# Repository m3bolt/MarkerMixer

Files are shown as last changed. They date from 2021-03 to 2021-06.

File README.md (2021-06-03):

<!-- PROJECT LOGO -->
<br />
<p align="center">
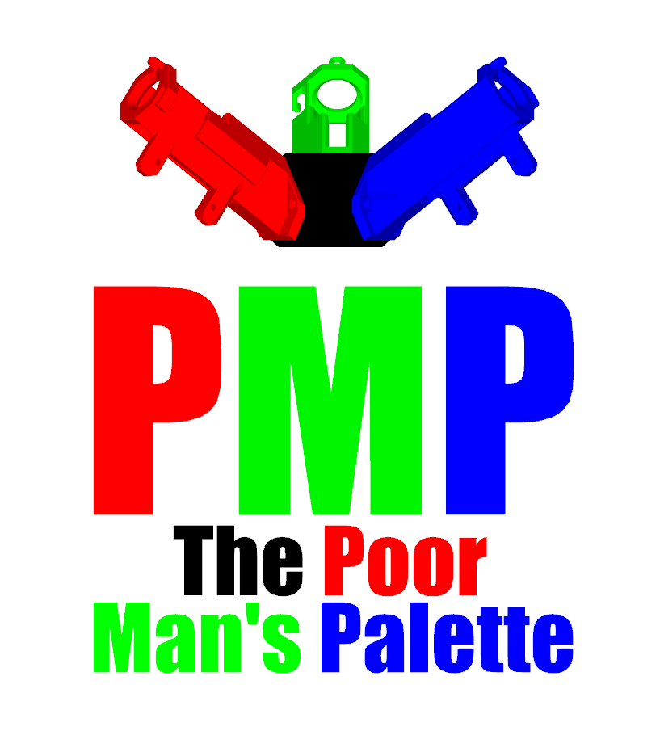
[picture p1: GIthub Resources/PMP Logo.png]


  <p align="center">
   Marker mixer/blender for dying filament with permanent markers before it enters the hotend
    <br />
	<a href="https://discord.gg/TchtRx5vXf"><strong>Join the PMP Discord </strong></a>
	·
    <a href="https://github.com/m3bolt/MarkerMixer/tree/main/STLs"><strong>Download STLs </strong></a>
	·
    <a href="https://www.youtube.com/watch?v=Sshl-3-f8Ro"><strong>PMP Demo Video </strong></a>
    ·
    <a href="https://github.com/m3bolt/MarkerMixer/issues">Report Bug</a>
    ·
    <a href="https://github.com/m3bolt/MarkerMixer/issues">Request Feature</a>
  </p>
</p>

<!-- ABOUT THE PROJECT -->
## About The Project

The Poor Mans Palette is designed to use servos to slide markers in out and of a central filament path. It is an evolution of and directly inspired by Youtuber Makers Muse who designed a manual version.

<!-- GETTING STARTED -->
## Getting Started

Using the Poor Mans Palette is easy, but it does require some setup. <a href="https://github.com/kackle1998">Viperian</a> has created <a href="https://docs.google.com/document/d/1HtXDXiIX8TrwlF5AgzMKKhFVkw75yK6E26BhG-3SkN0/edit"><strong>Google Doc Instructions</strong></a> for new users to set up and use their PMP. 

You will need some electronics and hardware:

| Part Name | Description | Quantity |
| --- | --- | --- |
| 3D Printer running Klipper | Klipper is required for servo control | 1 |
| Arduino (Nano or Uno)  | Used by Klipper to address servo pins  | 1 |
| 5v 1A+ Power Supply | Necessary to power servos, barrel jack recommended | 1 |
| M3 x 10mm screw | To secure Marker Holder to Marker Hub | 6 |
| M3 x 12mm screw | To hold the marker in in the Marker Slider | 3 |
| M3 Locknut | To secure Marker Screw Cap to 12mm screw | 3 | 
| M3 x 16mm screw | To mount Marker Hub to your printers Hub Mount | 3 |
| Breadboard or Perfboard | Used for wiring servos to the Arduino | 1 |
| 3-pin DUPONT headers | For plugging the servos into your breadboard or perfboard | 3 |
| SG90 Servo Motor | Used to extend and retract the markers | 3 |
| SG90 Servo mounting screws | Usually included with your SG90, these secure the servo to the Marker Body | 6 |

The following are the STLs required for a 3 marker setup and the quantity of each required: 

| Part Name | Notes | Quantity |
| --- | --- | --- |
| PMP_MarkerHub_R1.stl | | 1 |
| PMP_MarkerBody_NumX_R1.stl | Requires supports! Print NoNum for no numbers or 1-3 for numbered versions. | 3 |
| PMP_MarkerSlider_Size_ID_R1.stl | 2 versions available, one with a smaller ID and one with a larger ID. Print one at a time to verify the size required! | 3 |
| PMP_ServoGear_Size_ID_R1.stl | 5 versions available with different IDs for the servo shaft. Print one at a time to verify the size required! | 3 |
| PMP_MarkerScrewCap_R1.stl | Optional thumb screw caps for the set screw holding the marker in the slider | 3 |

Hub mounts to follow for some machines. 

In theory you can stack PMPs on top of eachother for even more color combinations and options, but we recommend starting with one set of 3. 

<!-- CONTACT -->
## Contact

If you need help or want to reach out, message Viperian and M3 Bolt on our 	<a href="https://discord.gg/TchtRx5vXf">Discord server.</a>

Project Link: https://github.com/m3bolt/MarkerMixer

<!-- LICENSE -->
## License

Distributed under the Creative Commons Attribution-NonCommercial-ShareAlike 4.0 license.

<!-- ACKNOWLEDGEMENTS -->
## Acknowledgements

* <a href="https://github.com/kackle1998">Viperian,</a> who originally had the idea of automatic slicer controlled marker switching and did all of the software/slicer parts of the project.
* <a href="https://www.youtube.com/channel/UCxQbYGpbdrh-b2ND-AfIybg">Makers Muse,</a> who showed a video of a manual marker filament dying system that inspired the project.
* <a href="https://github.com/m3bolt">M3 Bolt,</a> who did most of the Fusion based CAD work for the project.

<!-- MARKDOWN LINKS & IMAGES -->
<!-- https://www.markdownguide.org/basic-syntax/#reference-style-links -->
[contributors-shield]: https://img.shields.io/github/contributors/github_username/repo.svg?style=for-the-badge
[contributors-url]: https://github.com/github_username/repo/graphs/contributors
[forks-shield]: https://img.shields.io/github/forks/github_username/repo.svg?style=for-the-badge
[forks-url]: https://github.com/github_username/repo/network/members
[stars-shield]: https://img.shields.io/github/stars/github_username/repo.svg?style=for-the-badge
[stars-url]: https://github.com/github_username/repo/stargazers
[issues-shield]: https://img.shields.io/github/issues/github_username/repo.svg?style=for-the-badge
[issues-url]: https://github.com/github_username/repo/issues
[license-shield]: https://img.shields.io/github/license/github_username/repo.svg?style=for-the-badge
[license-url]: https://github.com/github_username/repo/blob/master/LICENSE.txt
[linkedin-shield]: https://img.shields.io/badge/-LinkedIn-black.svg?style=for-the-badge&logo=linkedin&colorB=555
[linkedin-url]: https://linkedin.com/in/github_username

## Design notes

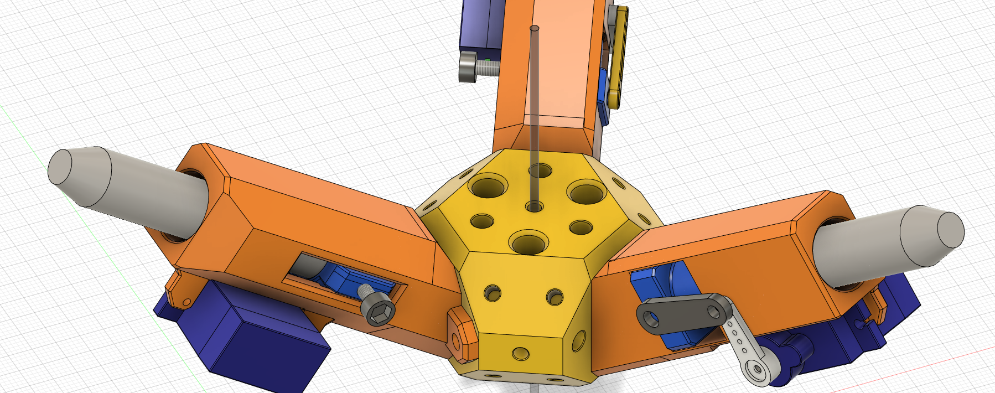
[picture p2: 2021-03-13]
MarkerBlender_v0.png

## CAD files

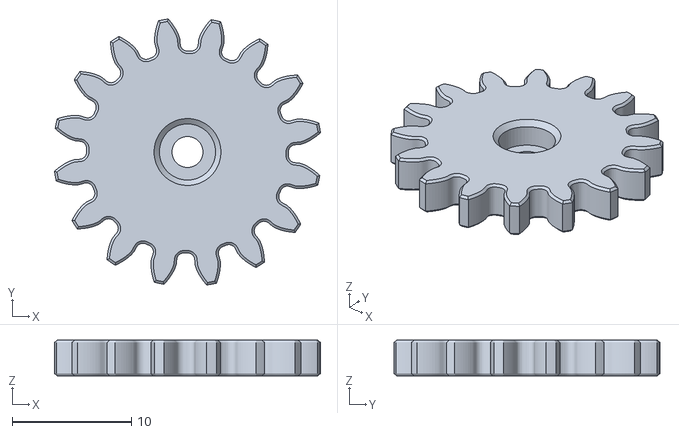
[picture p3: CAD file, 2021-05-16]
STLs/ServoGear/PMP_ServoGear_ExtraSmall_ID_R1.stl.stl
22.3 x 22.3 x 3.00

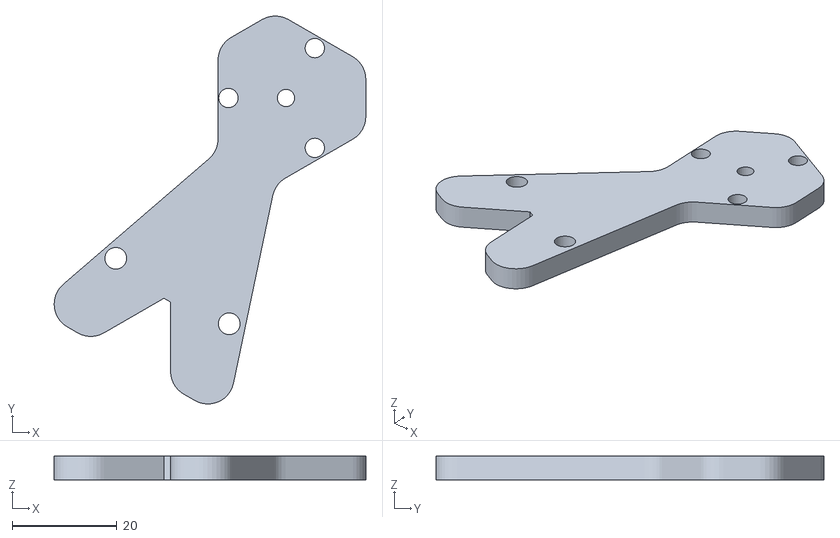
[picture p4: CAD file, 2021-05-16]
STLs/Hub Mounts/Hub_Mount_TopOfZ_V1.STL
59.5 x 74.1 x 4.50

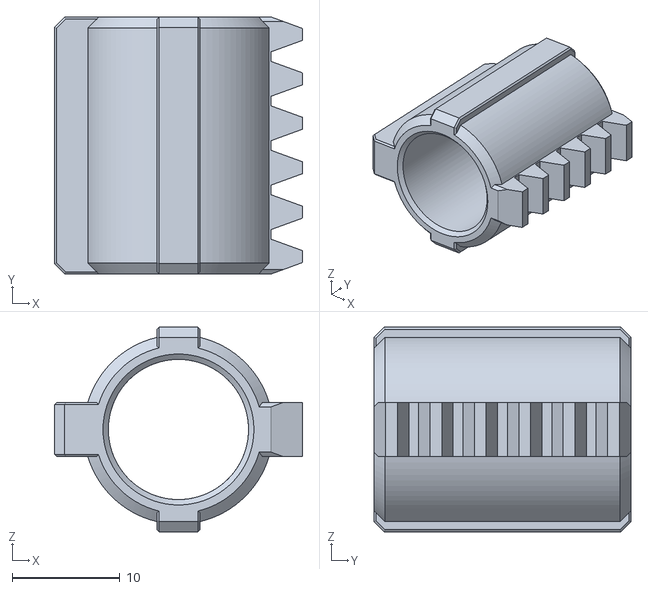
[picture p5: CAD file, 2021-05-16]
STLs/MarkerSlider/PMP_MarkerSlider_Smaller_ID_R1.stl
23.0 x 23.8 x 19.0

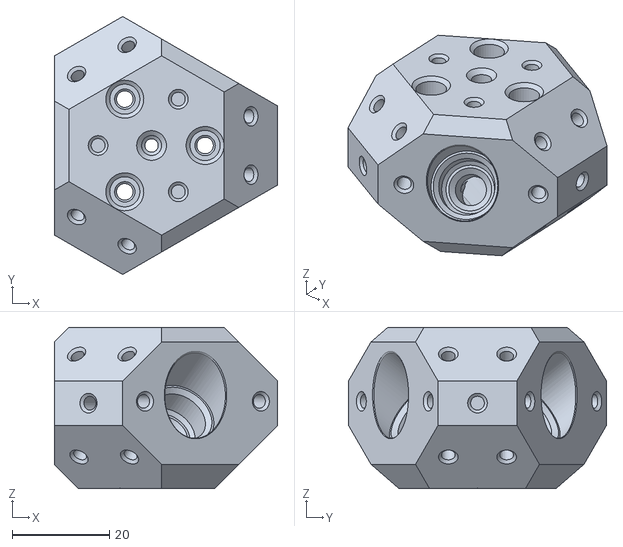
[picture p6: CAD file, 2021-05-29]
STLs/PMP_MarkerHub_R1.stl
45.9 x 53.0 x 33.1

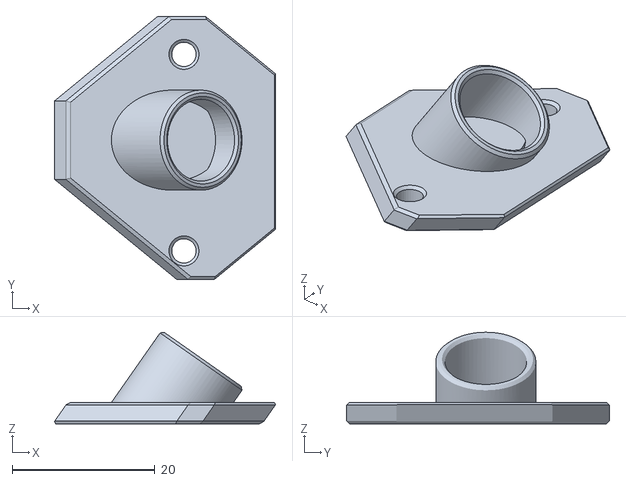
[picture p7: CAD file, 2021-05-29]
STLs/PMP_MarkerBlank_R1.stl
30.9 x 36.8 x 12.8

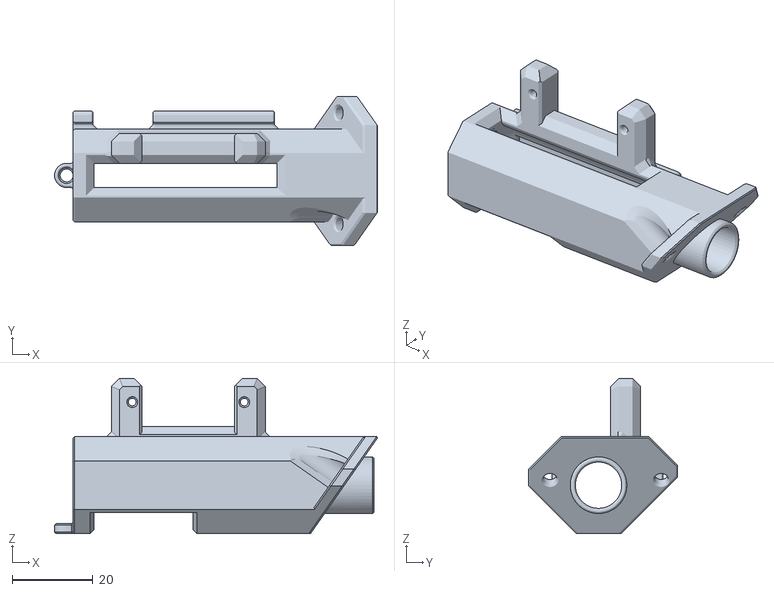
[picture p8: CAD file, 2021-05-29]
STLs/PMP_MarkerBody_NoNum_R1.stl
79.9 x 36.8 x 38.5

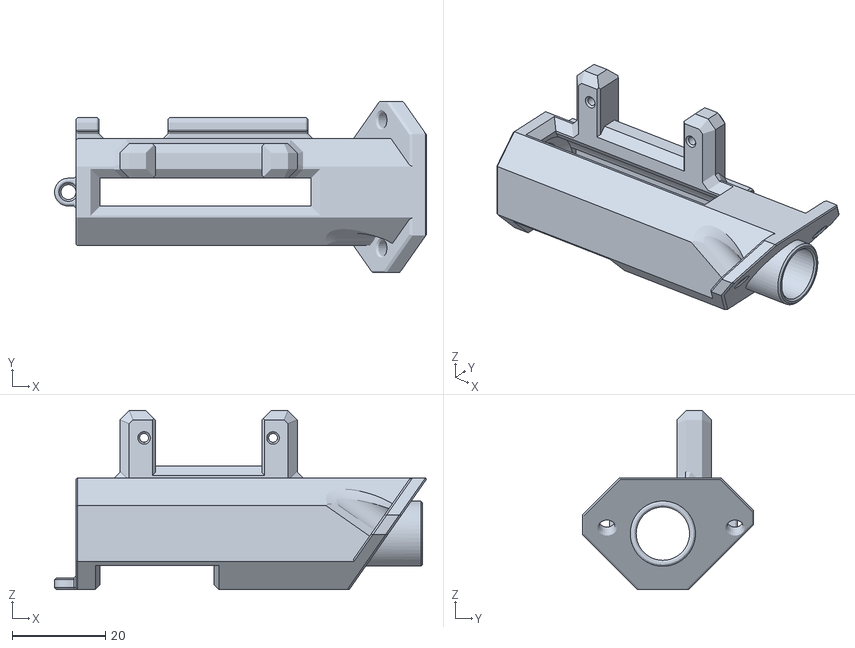
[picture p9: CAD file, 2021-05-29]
STLs/PMP_MarkerBody_Num2_R1.stl
79.9 x 36.8 x 38.5

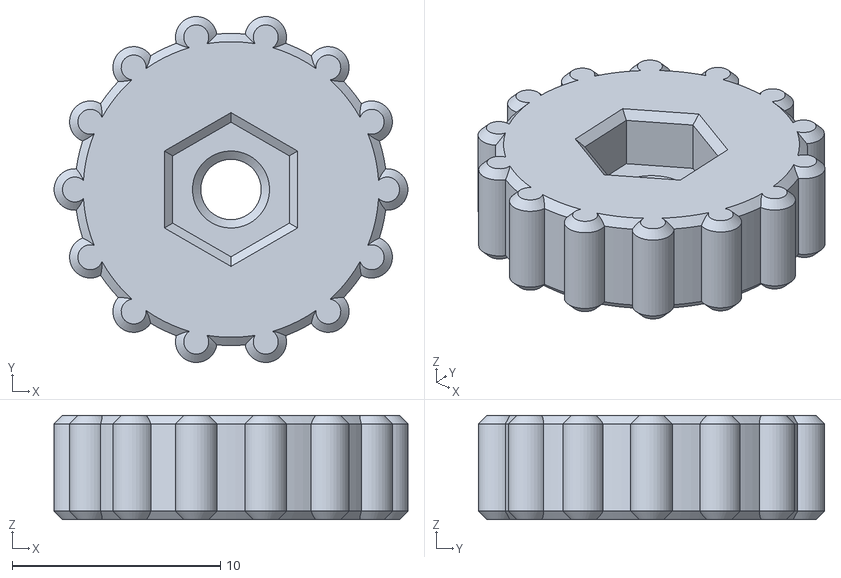
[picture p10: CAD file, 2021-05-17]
STLs/PMP_MarkerScrewCap_R1.stl
17.0 x 16.6 x 5.00

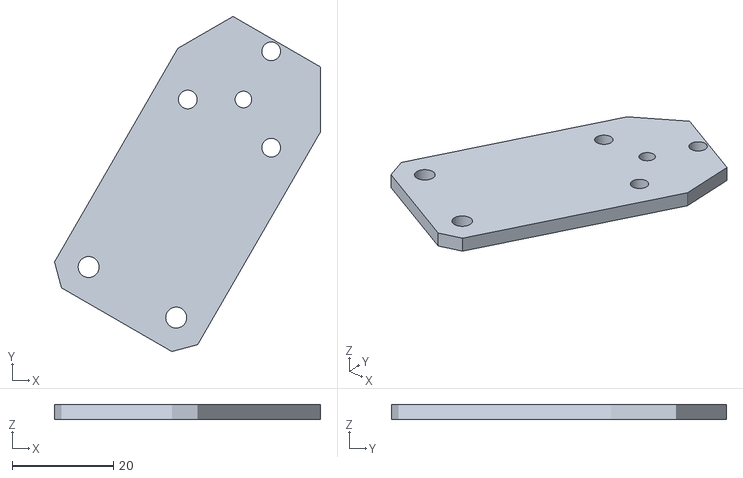
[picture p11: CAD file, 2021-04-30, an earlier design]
STLs/Hub Mounts/Hub_Mount_TopOfZ_V0.STL
52.6 x 66.3 x 3.00

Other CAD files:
STLs/MarkerSlider/PMP_MarkerSlider_Larger_ID_R1.stl
STLs/ServoGear/PMP_ServoGear_Extra-Large_ID_R1.stl
STLs/ServoGear/PMP_ServoGear_Medium_ID_R1.stl.stl
STLs/ServoGear/PMP_ServoGear_Small_ID_R1.stl.stl
STLs/PMP_MarkerBody_Num3_R1.stl
STLs/ServoGear/PMP_ServoGear_Large_ID_R1.stl.stl
STLs/PMP_MarkerBody_Num1_R1.stl

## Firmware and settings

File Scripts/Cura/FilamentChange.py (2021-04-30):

# Magic Marker Mixer
 #Github: https://github.com/m3bolt/MarkerMixer
 #Designers:
 #Code: https://github.com/kackle1998 
 #Mech Design: https://github.com/m3bolt/ , https://github.com/kackle1998 
 #WIP
 #Initial Arduino+Cura proof of concept for 1in-1out multicolor 3D Printing

from typing import List
from ..Script import Script

class FilamentChange(Script):

    _layer_keyword = ";LAYER:"

    def __init__(self):
        super().__init__()

    def getSettingDataString(self):
        return """{
            "name":"The Magic Marker Mixer",
            "key": "FilamentChange",
            "metadata": {},
            "version": 2,
            "settings":
            {
                "layer_number_S1E":
                {
                    "label": "Servo One Engage Layer",
                    "description": "Layer height where servo one turns on. Specify multiple color changes with a comma.",
                    "unit": "",
                    "type": "str",
                    "default_value": "1"
                },
                "layer_number_S1R":
                {
                    "label": "Servo One Retract Layer",
                    "description": "Layer height where servo one turns off. Specify multiple color changes with a comma.",
                    "unit": "",
                    "type": "str",
                    "default_value": "2"
                },
                "layer_number_S2E":
                {
                    "label": "Servo Two Engage Layer",
                    "description": "Layer height where servo two turns on. Specify multiple color changes with a comma.",
                    "unit": "",
                    "type": "str",
                    "default_value": "1"
                },
                "layer_number_S2R":
                {
                    "label": "Servo Two Retract Layer",
                    "description": "Layer height where servo two turns off. Specify multiple color changes with a comma.",
                    "unit": "",
                    "type": "str",
                    "default_value": "2"
                },
                "layer_number_S3E":
                {
                    "label": "Servo Three Engage Layer",
                    "description": "Layer height where servo three turns on. Specify multiple color changes with a comma.",
                    "unit": "",
                    "type": "str",
                    "default_value": "1"
                },
                "layer_number_S3R":
                {
                    "label": "Servo Three Retract Layer",
                    "description": "Layer height where servo three turns off. Specify multiple color changes with a comma.",
                    "unit": "",
                    "type": "str",
                    "default_value": "2"
                }
                
            }
        }"""

    def execute(self, data: List[str]):
        """Inserts the filament change g-code at specific layer numbers.
        :param data: A list of layers of g-code.
        :return: A similar list, with filament change commands inserted.
        """
        #Servo1
        layer_nums_S1E = self.getSettingValueByKey("layer_number_S1E")
        layer_nums_S1R = self.getSettingValueByKey("layer_number_S1R") 
        servo1_engage = "MarkerOneEngage"
        servo1_retract = "MarkerOneRetract"
        servo1_engage = servo1_engage + " ; engage servo one \n"
        servo1_retract = servo1_retract + " ; retract servo one \n"
        #Servo2
        layer_nums_S2E = self.getSettingValueByKey("layer_number_S2E")
        layer_nums_S2R = self.getSettingValueByKey("layer_number_S2R") 
        servo2_engage = "MarkerTwoEngage"
        servo2_retract = "MarkerTwoRetract"
        servo2_engage = servo2_engage + " ; engage servo two \n"
        servo2_retract = servo2_retract + " ; retract servo two \n"
         #Servo3
        layer_nums_S3E = self.getSettingValueByKey("layer_number_S3E")
        layer_nums_S3R = self.getSettingValueByKey("layer_number_S3R") 
        servo3_engage = "MarkerThreeEngage"
        servo3_retract = "MarkerThreeRetract"
        servo3_engage = servo3_engage + " ; engage servo three \n"
        servo3_retract = servo3_retract + " ; retract servo three \n"

        #Servo1
        layer_targets_S1E = layer_nums_S1E.split(",")
        if len(layer_targets_S1E) > 0:
            for layer_num_S1E in layer_targets_S1E:
                try:
                    layer_num_S1E = int(layer_num_S1E.strip()) + 1 #Needs +1 because the 1st layer is reserved for start g-code.
                except ValueError: #Layer number is not an integer.
                    continue
                if 0 < layer_num_S1E < len(data):
                    data[layer_num_S1E] = servo1_engage + data[layer_num_S1E]

        layer_targets_S1R = layer_nums_S1R.split(",")
        if len(layer_targets_S1R) > 0:
            for layer_num_S1R in layer_targets_S1R:
                try:
                    layer_num_S1R = int(layer_num_S1R.strip()) + 1 #Needs +1 because the 1st layer is reserved for start g-code.
                except ValueError: #Layer number is not an integer.
                    continue
                if 0 < layer_num_S1R < len(data):
                    data[layer_num_S1R] = servo1_retract + data[layer_num_S1R]

        #Servo2
        layer_targets_S2E = layer_nums_S2E.split(",")
        if len(layer_targets_S2E) > 0:
            for layer_num_S2E in layer_targets_S2E:
                try:
                    layer_num_S2E = int(layer_num_S2E.strip()) + 1 #Needs +1 because the 1st layer is reserved for start g-code.
                except ValueError: #Layer number is not an integer.
                    continue
                if 0 < layer_num_S2E < len(data):
                    data[layer_num_S2E] = servo2_engage + data[layer_num_S2E]

        layer_targets_S2R = layer_nums_S2R.split(",")
        if len(layer_targets_S2R) > 0:
            for layer_num_S2R in layer_targets_S2R:
                try:
                    layer_num_S2R = int(layer_num_S2R.strip()) + 1 #Needs +1 because the 1st layer is reserved for start g-code.
                except ValueError: #Layer number is not an integer.
                    continue
                if 0 < layer_num_S2R < len(data):
                    data[layer_num_S2R] = servo2_retract + data[layer_num_S2R]
        
        #Servo3
        layer_targets_S3E = layer_nums_S3E.split(",")
        if len(layer_targets_S3E) > 0:
            for layer_num_S3E in layer_targets_S3E:
                try:
                    layer_num_S3E = int(layer_num_S3E.strip()) + 1 #Needs +1 because the 1st layer is reserved for start g-code.
                except ValueError: #Layer number is not an integer.
                    continue
                if 0 < layer_num_S3E < len(data):
                    data[layer_num_S3E] = servo3_engage + data[layer_num_S3E]
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

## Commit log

2021-03-13 v0 STLs
    v0 files
    [MarkerBlender_Slider_v0.stl]
2021-03-13 v0 STLs
    [MarkerBlender_Body_v0.stl, MarkerBlender_Hub_HexNuts_v0.stl, MarkerBlender_Hub_Inserts_v0.stl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]
2021-03-13 v0 CAD assembled
2021-03-17 Added new v1 parts
    v1 uses a rack and pinion style system for better torque.
    [MarkerBlender_Body_v1.stl, MarkerBlender_Slider_Rack_v1.stl]
2021-03-17 Added new v1 parts
    [MarkerBlender_ServoGear_v1.stl]
2021-03-17 Added v1 longer slide body
    [MarkerBlender_Body_v1.stl]
2021-03-17 Code for controlling via High/Low signals
    Pins optimized for Nano wiring
2021-03-18 CuraFirstFunctionalDraft
    Replace the old filamentchange script with this one. No idea why I can't make a new script
    [FilamentChange.py]
2021-03-18 High/Low pin level control file
2021-04-21 Add v0 Drop In Nut Hub
    [MarkerBlender_Hub_DropInNuts_v0.stl]
2021-04-24 Tolerance adjustments to drop in nut hub
    [MarkerBlender_Hub_DropInNuts_v1.stl]
2021-04-24 v1 drop in hub added, v0 deleted
    [MarkerBlender_Hub_DropInNuts_v0.stl]
2021-04-26 WIP Test files for tolerance changes
    [Gear_Diameter_Smaller_100micron.stl, Gear_Diameter_Smaller_200micron.stl, Gear_Diameter_Smaller_300micron.stl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]
2021-05-13 Added solenoid files
    [MakerBlender_Solenoid_BodyTop_v0.stl, MakerBlender_Solenoid_Body_v0.stl, MakerBlender_Solenoid_Slider_v0.stl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]
2021-05-13 Added solenoid version CAD picture
2021-05-15 v1 solenoid STLs
    [MakerBlender_Solenoid_BodyTop_v0.stl, MakerBlender_Solenoid_BodyTop_v1.stl, MakerBlender_Solenoid_Body_v0.stl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]
2021-05-17 Added thumb screw cap
    [ThumbScrewCap.stl]
2021-05-29 Upload PMP Release R1 files
    [Hub_Mount_TopOfZ_V0.STL, Hub_Mount_TopOfZ_V1.STL, PMP_MarkerBlank_R1.stl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]
2021-05-29 Add R1 STLs
    [PMP_MarkerScrewCap_R1.stl]
2021-05-29 Delete Circuitry/3Servo1Nano/3servo1nano directory
    No longer needed
    [3servo1nano.kicad_pcb, 3servo1nano.sch]
2021-05-29 Delete Scripts/Arduino directory
    No longer used
